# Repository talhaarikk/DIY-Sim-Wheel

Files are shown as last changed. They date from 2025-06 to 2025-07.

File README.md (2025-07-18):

# DIY Sim Wheel
## Purpose
The purpose of this project is to make a powerful sim racing wheel cheaply (also i like doing this kind of stuff). But actualy the main reason i started this project was that i didn't want to buy a logitech g29 (g29 because it is the most common, known, reliable and cheap model on the market). Because the g29 was made of too much plastic, the torque was not at the level i wanted and the size of the steering wheel was not enough for me. That's why i focused on these issues in my own design. Below you can find all the details of the steering wheel.  
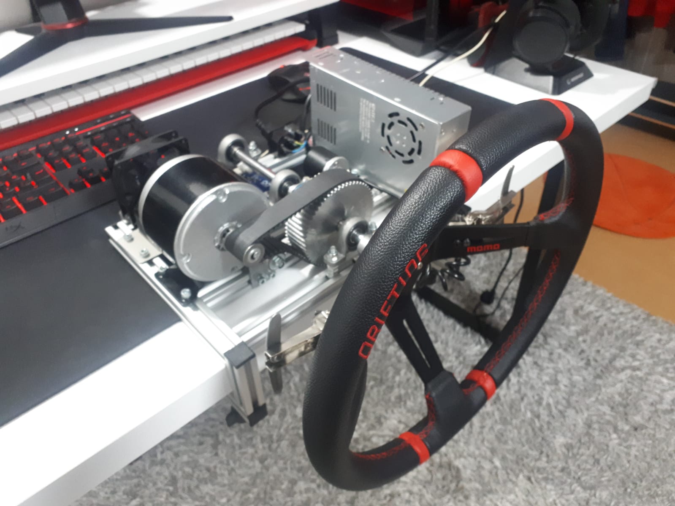
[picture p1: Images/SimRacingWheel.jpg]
Sim Racing Wheel
  
You can find more photos of the sim steering wheel in the Images/Steering_Wheel folder.  

## Motor
To be honest, when i started the project, i didn't want to make a design like the one below. I had in mind to make a direct drive sim wheel by purchasing a stepper motor with an encoder and a stepper motor driver. However, since the prices of these parts were higher ($110 for stepper motor and $110 for driver) and i couldn't see an example of a sim wheel made using with stepper motor, i decided to make this project with the motor below. My advice to you is that if you don't have a budget problem and still want to make your own sim wheel, you should continue with a servo motor. If I had used such a motor, i wouldn't have bothered with the gears, shaft or frame in this project.  
As an motor, i chose this motor which is originally used in scooters.  
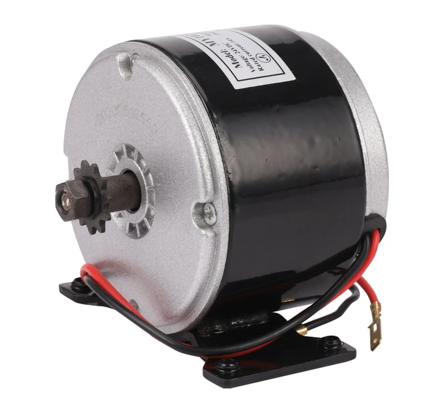
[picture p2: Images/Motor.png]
Motor
  
Brushed DC motor. Model: MY1025  
Works with 24V and 14A (so its 250W). Also 2750RPM (actually, what i paid attention to was not the rpm but the torque).  
I think this motor will be powerful enough for the steering wheel. If you want, you can do the project by using 2 smaller motor or even using 2 of this motor. Although i didn't need such a thing.
## Power Supply

When choosing a power supply, i preferred a 24V and 15A power supply. Since the motor is 250 watt, the watt of the power supply should be slightly higher (in this case 300W).  
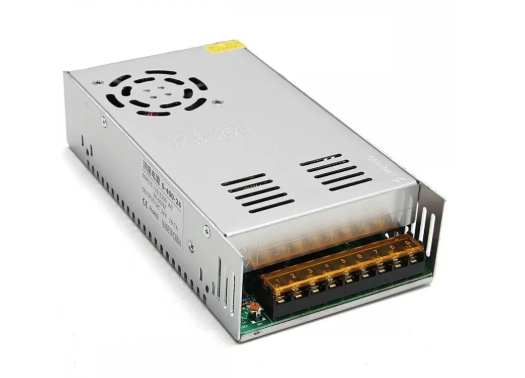
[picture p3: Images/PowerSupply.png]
Power Supply
  

## Gears
There are 4 gears in the steering wheel, one between the shaft and the motor and one between the shaft and the encoder. I recommend that you make sure that the gears are made of aluminum so that you can drill the holes and that they are not too heavy. Even though the gears were made of aluminum, the most challenging part of this project was the holes i drilled to mount the gears on the shaft. These gears mounted on the shaft should not be fixed with any gaps in order to ensure a healthy transmission. My method of fixing them was to drill screw holes in the gears and flatten the areas where the screws were tightened on the shaft to prevent them from slipping.  
  -**Components for the motor:**  
60-5M-25-AL (on the shaft)  
12-5M-25-AL (on the motor)  
410-5M-25 (pulley)  
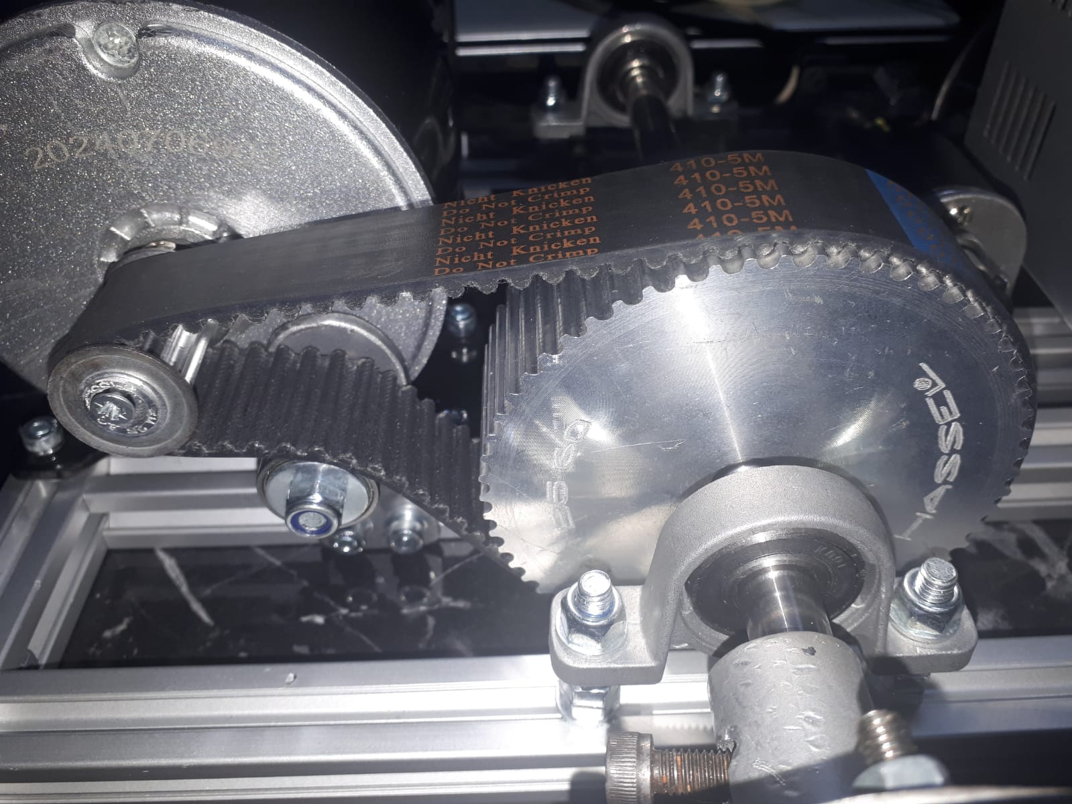
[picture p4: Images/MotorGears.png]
Motor Gears
  
The torque produced by the motor itself was around 0.87 nm. With the 60/12 gear ratio, this value was multiplied by 5, theoretically reaching 4.35 nm (i did not measure this value experimentally). This value is approximately twice that of the Logitech G29.  
  -**Components for the encoder:**  
12-3M-09-AL (on the encoder)  
30-3M-09-AL (on the shaft)  
192-3M-09 (pulley)  
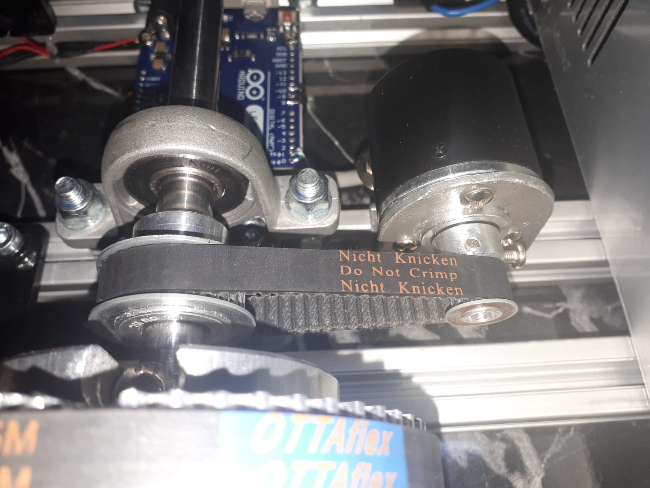
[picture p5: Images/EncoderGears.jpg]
Encoder Gears
  
Since the encoder itself will not transfer any torque and will only rotate the sensor, i did not feel the need to use a stronger belt as in the encoder. The encoder was reading 600 times in 1 turn. With the 12/30 gear ratio, this value increased by 2.5 times. Now the encoder is reading 1500 times in 1 turn. You can interpret this value as reading 1 every 0.25 degrees of steering wheel rotation, which is quite sufficient.  
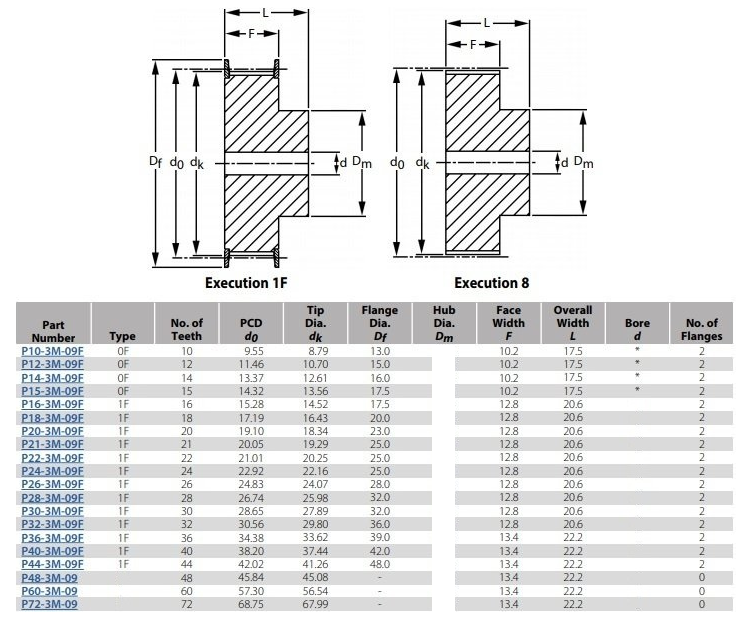
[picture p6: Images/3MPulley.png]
3M Pulley
  
Table of pulleys for size 3M-09. Unfortunately i couldn't find the one for 5M-25.  

## Other Hardwares
  -**Shaft**  
When talking about other components, i must first mention the shaft. The shaft length is 26 cm and its diameter is 12 mm. The material is stated as induction shaft, but if i were to choose the shaft again, i would definitely not choose this material. Drilling holes on it to fix the gears was a complete torture. At least it is solid now.  
  -**Bearing Housing**  
I used the following bearing to hold this shaft. Model number KP001. There are 3 of them holding the shaft, but you can also use 2 if you want.  
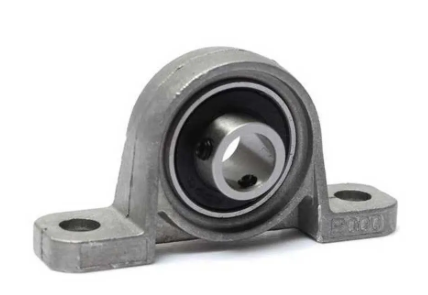
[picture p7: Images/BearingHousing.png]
Bearing Housing
  
  -**Belt Tensioner**  
For the belt tensioner, i used 3 bearings on a piece i cut from a metal plate. This piece both makes assembly easier and helps adjust the tension of the belt.  
  -**Steering Wheel**  
This is a after market steering wheel. Any one you like will do.  
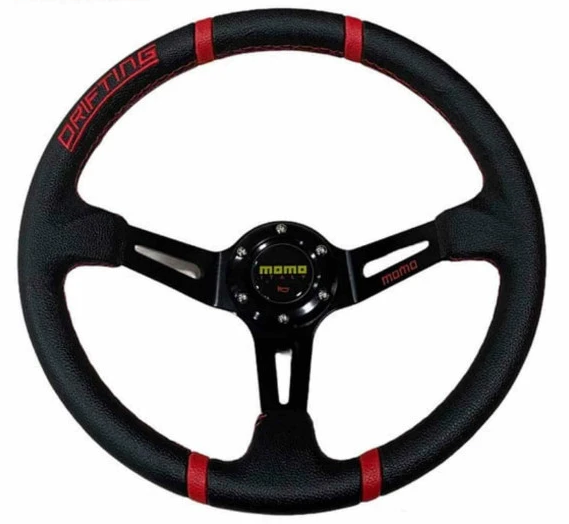
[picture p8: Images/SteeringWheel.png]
Steering Wheel
  
  -**Steering Wheel Hub**  
I made it by welding a pipe to a round metal plate. If you can, a 3D printed part would work just fine too.  
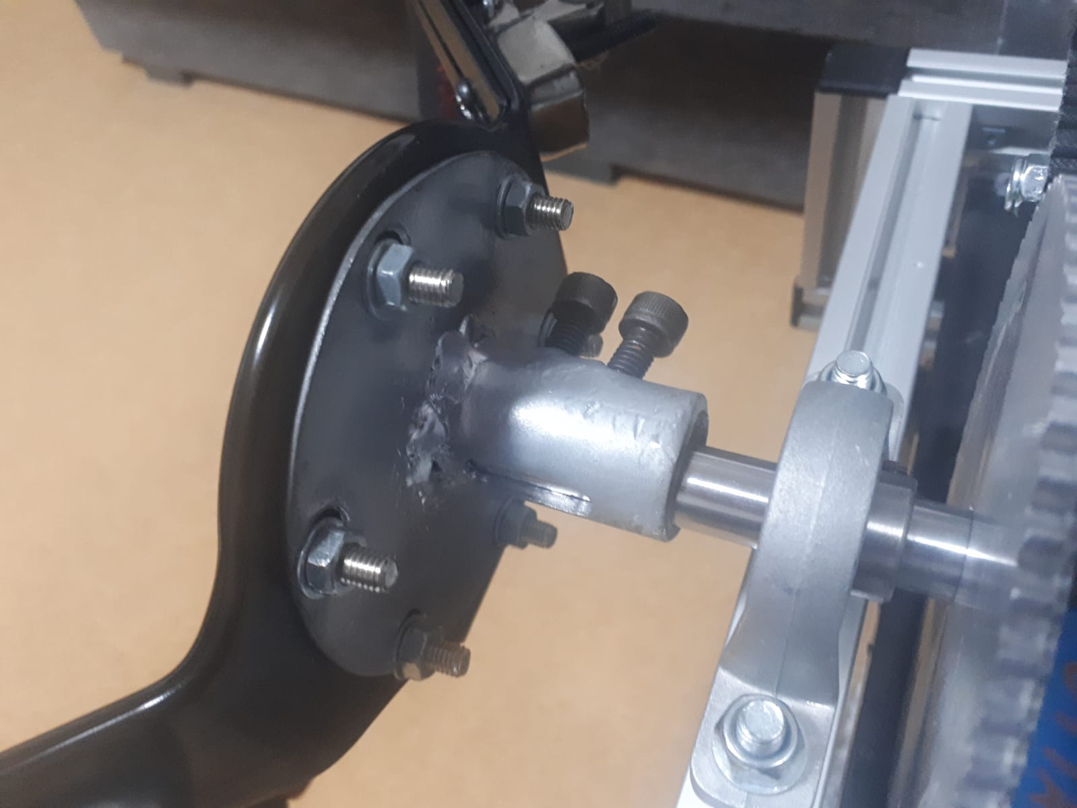
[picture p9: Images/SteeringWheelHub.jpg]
Steering Wheel Hub
  

## Frame
I used aluminum sigma profile in the cage structure that helps bring all the pieces together. Sigma profile width and length is 20 mm. The lengths of all the sigma profiles i use are as follows.  
280 mm x 4  
220 mm x 2  
70 mm x 2  
50 mm x 2  
The 70 and 50 mm pieces are a solution i found to fix the system to the table. If you have a sim racing cockpit, you won't need this part to fix it.  
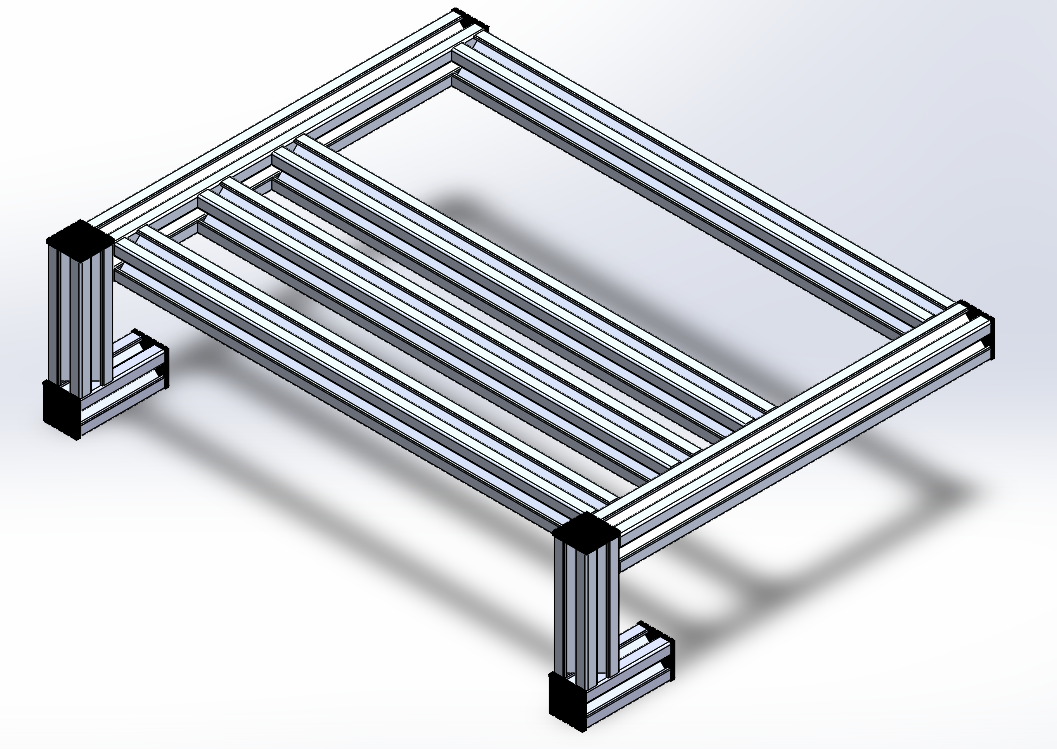
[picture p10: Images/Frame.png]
Frame
  
The bolts on the profile were used with imbus bolts and t-nuts for fixing. I used hidden corner joints to connect the profiles to each other. I also put caps on the ends of the profiles so that they would not look ugly.  

## Electronics
  -**Board**  
I chose Arduino Leonardo as the card in the project. Arduino Pro Micro will also do the same job, but Arduino Uno is not suitable for this project.  
  -**Motor Driver**  
I used the BTS7960B driver as the motor driver. This driver is enough to feed the motor, but i want to warn you about something. If the connections of this driver are made and the motor and encoder connections are not made yet, do not try to run the motor from the software. Don't ask how i know (i burned 2 of them).  
  -**Fan**  
Actually, i did not see that the motor and driver got very hot during use, but i still positioned a 5V computer fan to cool the motor and driver.  

## Design
I made the entire design using solidworks. I also found the gear diameters and belt lengths thanks to this program. You can find all the details of the project in these files. All files in the solidworks files section.  
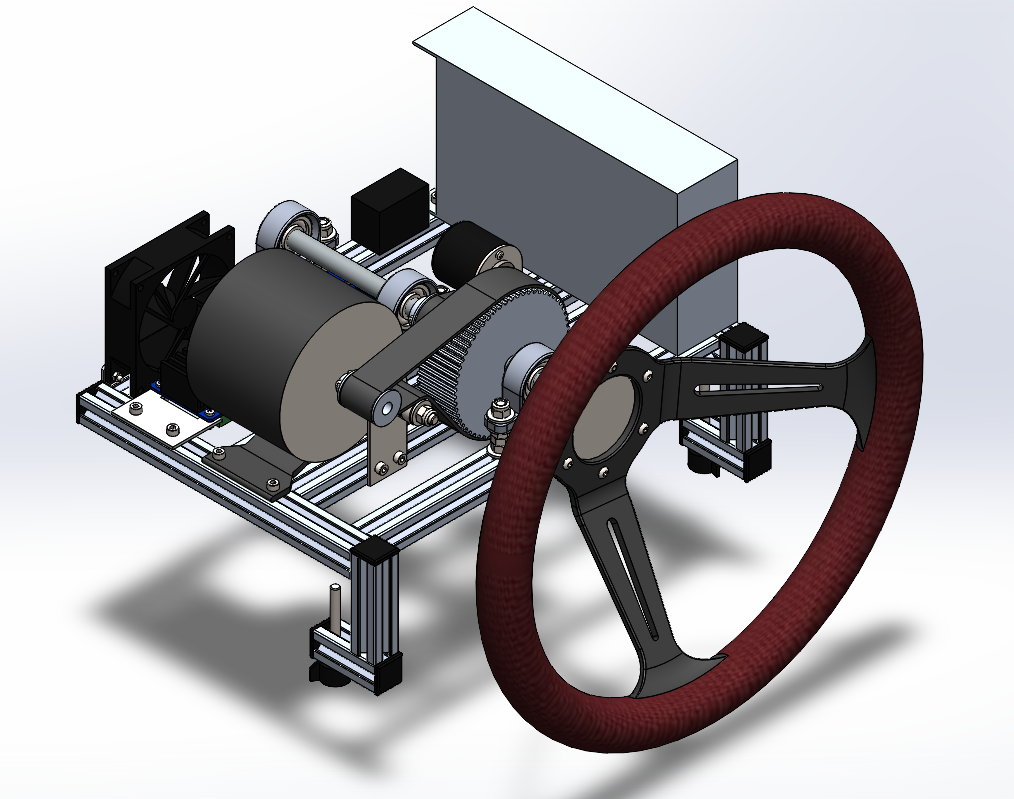
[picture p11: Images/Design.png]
Design
  
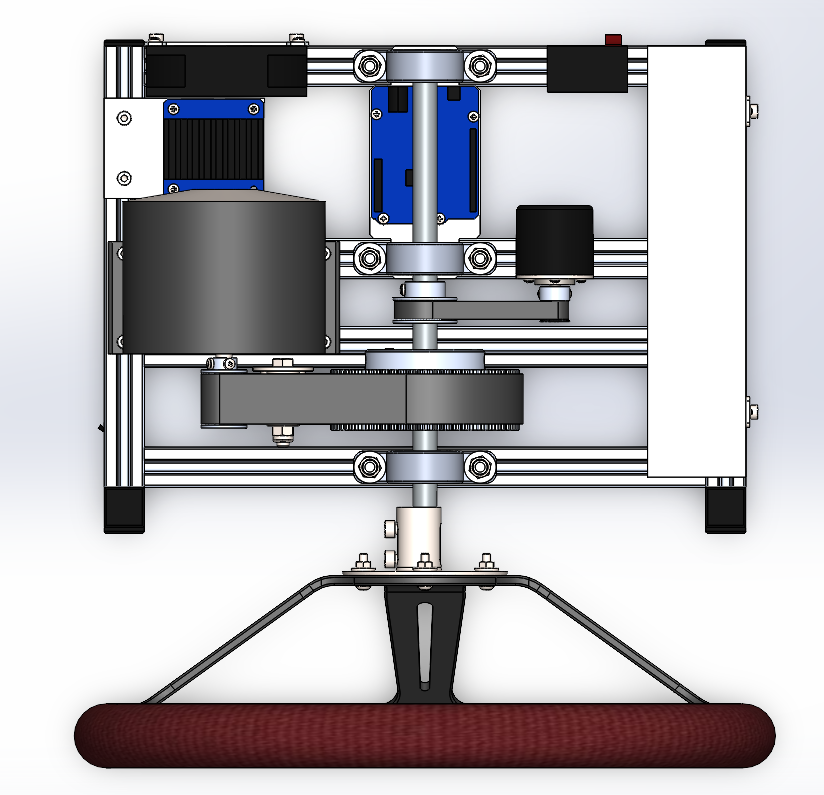
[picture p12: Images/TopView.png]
Top View
  
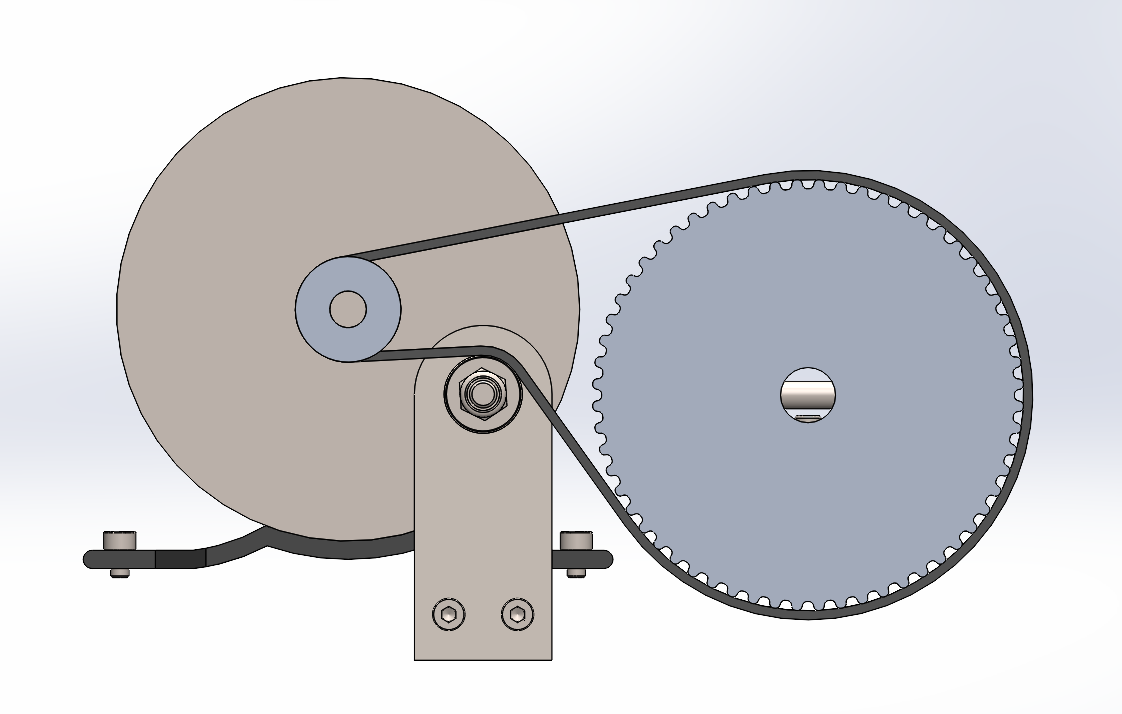
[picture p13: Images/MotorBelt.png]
Motor Belt
  
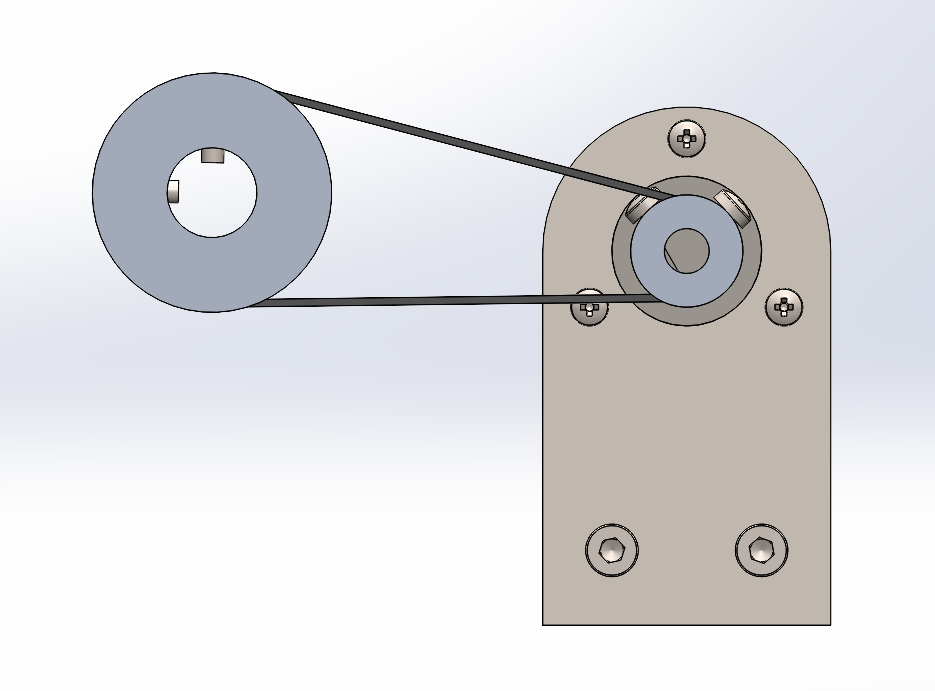
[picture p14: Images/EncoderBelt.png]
Encoder Belt
  

## Assembly
It is a bit difficult to assemble this whole system. The following steps can make it easier for you to understand the assembly.  
1-Assemble the entire frame structure and the elements on it except the encoder holder and the belt tensioner.  
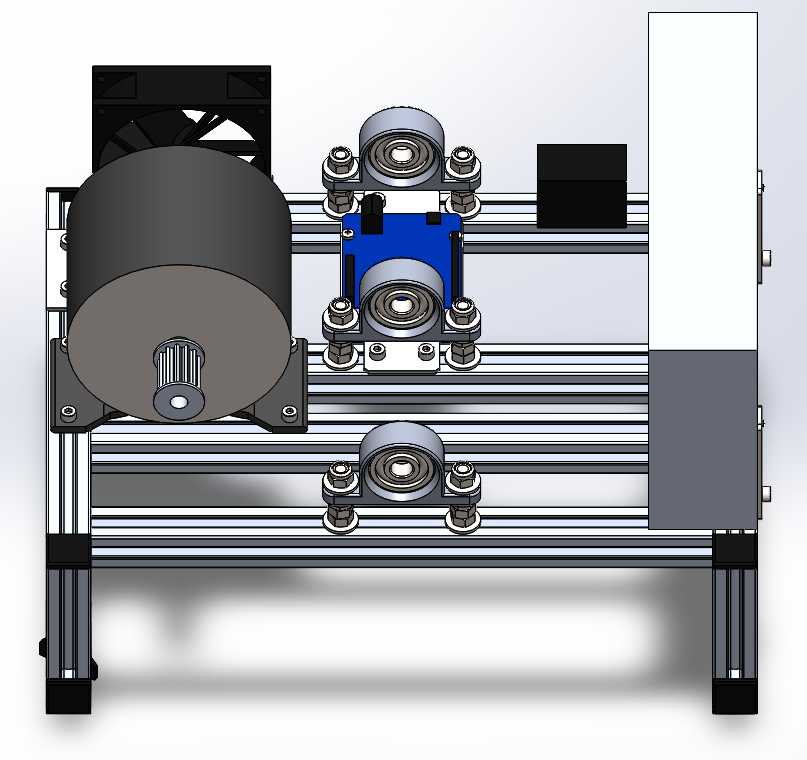
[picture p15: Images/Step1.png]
Step 1
  
2-Insert the shaft through the bearings one by one. Make sure the gears and belts remain inside the shaft when doing this.  
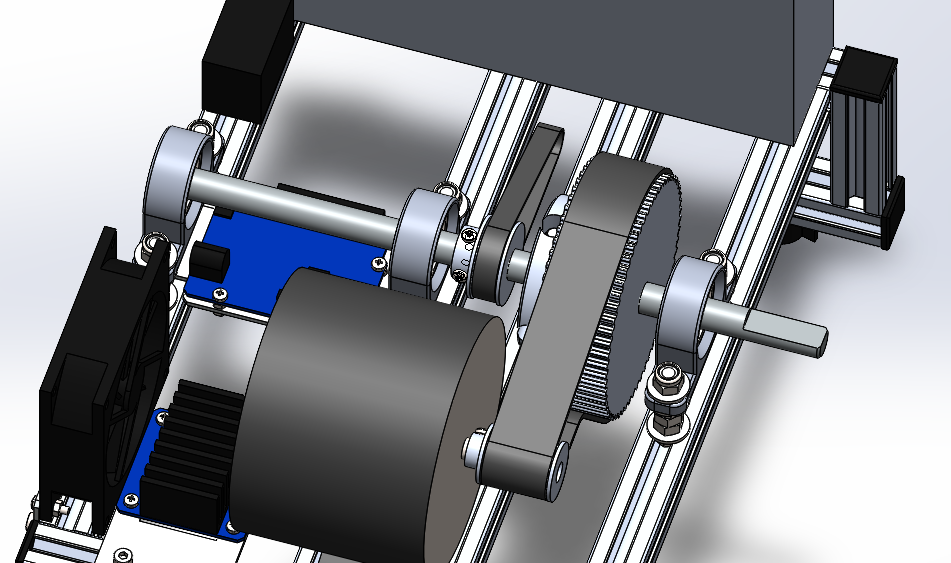
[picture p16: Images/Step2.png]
Step 2
  
3-Then tighten the bolts of the gears and connect them to the shaft.  
4-Install the encoder and belt tensioner. Then push these elements until the belts are at the appropriate tension and then tighten them.  
5-Finally, attach the steering wheel to the shaft.  

## Pedal Shifters
The reason i opened a separate title for the pedal shifter was that i decided to add it to the steering wheel after the whole project was finished. So this part is not in solidworks file. You don't have to do this part if you don't want to.  
I simply used a cabinet hinge as a pedal shifter. After cutting it to the required dimensions, i added a switch that is triggered when pressed. I made the connection to the arduino with a braided cable so that it can withstand the rotation of the steering wheel. This cable is removable and pluggable, so i can remove it when using manual gear. Other than these, there is nothing difficult about this part. You can understand how it works from the photo below.  
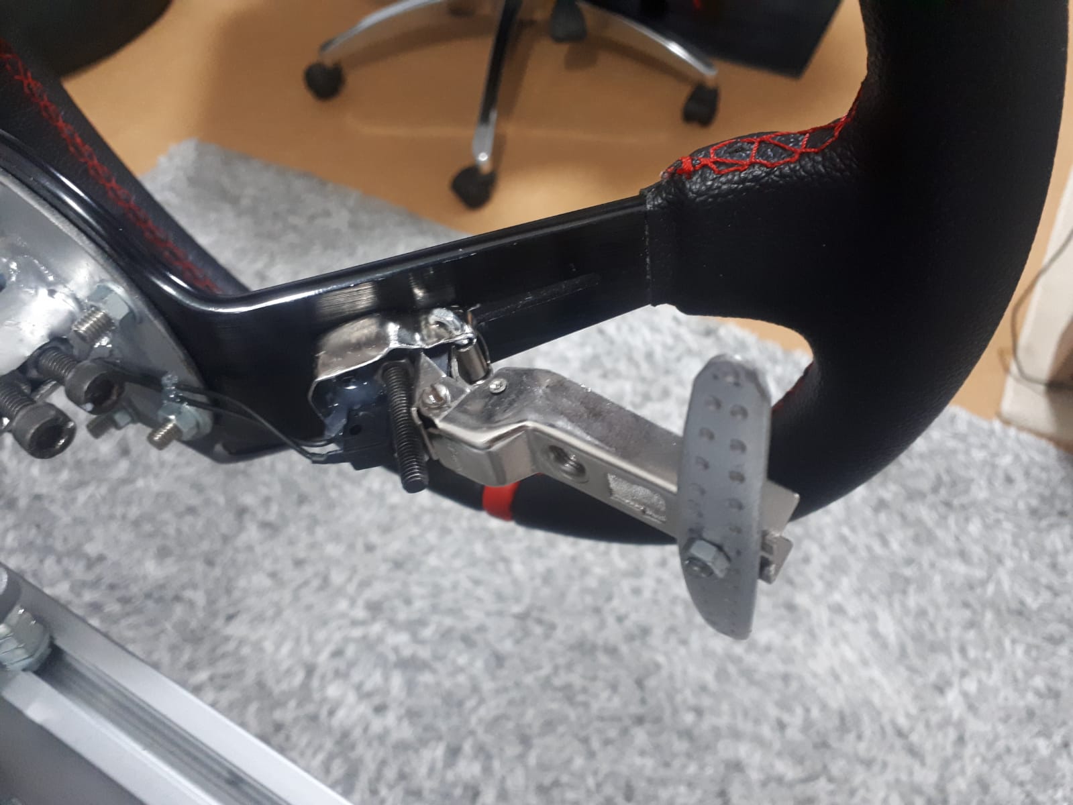
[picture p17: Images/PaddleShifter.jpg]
Paddle Shifter
  

## Wiring Diagram
The wiring is completely taken from the video below.  
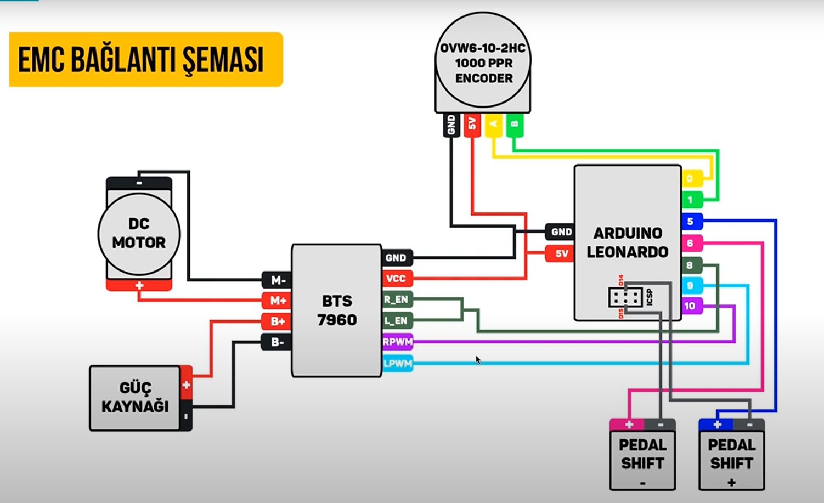
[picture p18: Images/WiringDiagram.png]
Wiring Diagram
  
The only difference in wiring is that you may need to reverse the motor + and - poles to the driver. That's what i had to do. Also in addition, i added an on/off switch and a power cable input to the + input of the power supply.  

## Software
Actually the first software i ran was the wheelconfig program but i couldn't get the system to work using this program. Also this program has a more complex schematic. That's why i preferred EMC software.  
The only thing i didn't do myself in this project and copied directly was the software. That's why i won't show how to set up the program, transfer it to arduino and make settings here. You can use the videos i put below to do these.  
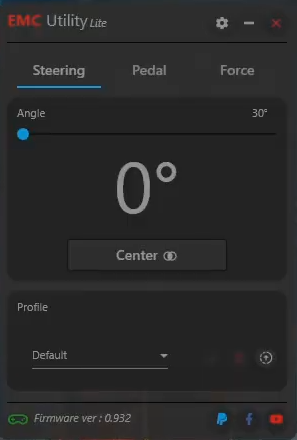
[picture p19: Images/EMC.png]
EMC
  
After installing the software, everything that needs to be done about the steering wheel is finished.  

## Cost
In this section, i will write the prices of the pieces in turkish lira. Since my purpose in doing my projects is completely up to my enjoyment, they are spread over a long period of time like 1-2 years. That's why prices and exchange rates are variable, but as of the date i did the project, you can think of 1 dollar as 30-40 turkish lira.  
Motor: 1700 tl  
Power supply: 600 tl  
Steering wheel: 1500 tl  
Encoder: 550 tl  
Arduino: 400 tl  
BTS7960b: 200 tl  
Gears: 1000 tl  
Other hardwares: 1000 tl  
Other electranics: 500 tl  
Total: 7450 tl  
Half price of g29.  

## Sources
Below are the videos that i watched to gain information when starting this project. I recommend that you watch them too.  
https://youtu.be/hbCjbCfUp0g?si=NynA37pT9rn3MCQu (for mechanical)  
https://youtu.be/FUZKslSwfaw?si=WwYVih52zpUwfXec (for electrical)  
https://youtu.be/L-FAyA0VQVQ?si=nJCx8VnmU1xidO3N  
https://youtu.be/nPorcXRC3Ns?si=enejoyd5WoKqs4ha  
https://youtu.be/aYYAbcPKN8g?si=kRVGH3cPVwXVqP0q  
https://youtu.be/gG_dbnKfH5Q?si=5sSKj9XNKsQQZj4X (example using stepper motor)  
https://youtu.be/_h417VxFmWQ?si=Obe5oXemXU2WvnzE (example using servo motor)  

## Conclusion
This project was an adventure that gave me a lot of knowledge while doing it (i can't say that i enjoyed it during the process). It was much more solid, powerful, cheap and high quality compared to other steering sets on the market. I hope i could contribute to your own projects. If you have any questions about the project, don't hesitate to ask me from talhaarik1965@gmail.com.

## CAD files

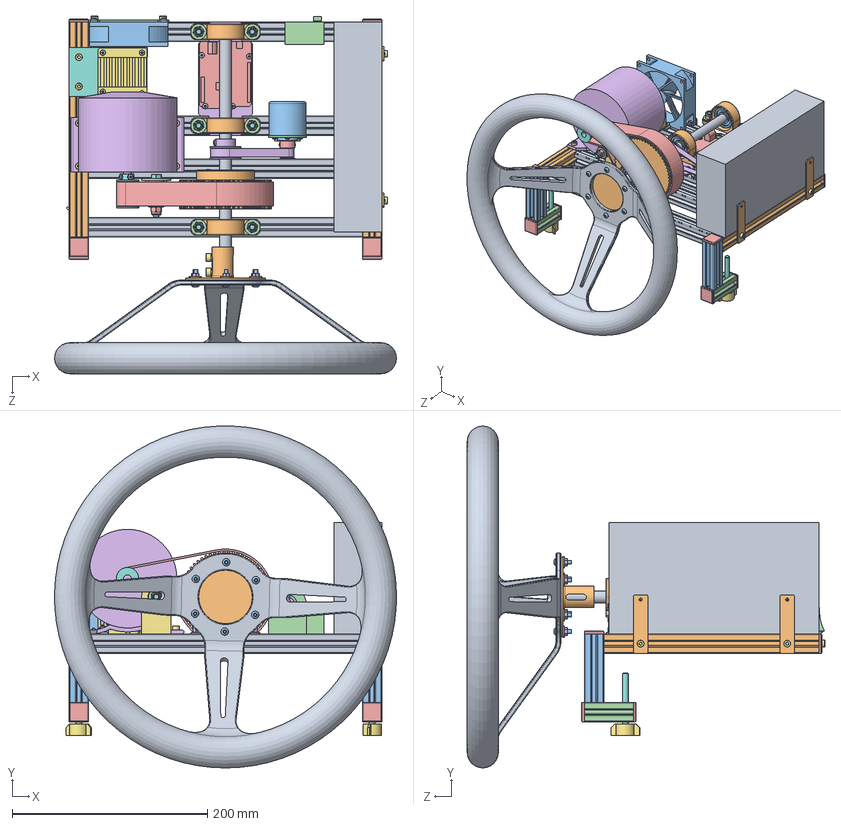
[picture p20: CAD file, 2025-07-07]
Solidworks Files/Assembly.SLDASM
349.9 x 349.8 x 366.0 mm
20x20 28cm Sigma Profile x 4
20x20 22cm Sigma Profile x 2
20x20 7cm Sigma Profile x 2
20x20 5cm Sigma Profile x 2
Sigma Cap x 8
hex nut style 1 gradeab_iso x 47
Table Mount x 2
hex bolt gradeb_iso x 9
Shaft
Bearing Housing x 3
instrument ball bearing_68_iso x 3
plain washer 10669 type nl_iso x 28
torque nut 01_iso x 7
Motor
socket head cap screw_iso x 23
12-5M-25-AL
pan head cross recess screw_iso x 20
60-5M-25-AL
Encoder
Encoder Holder
12-3M-09-AL
30-3M-09-AL
Belt Tensioner
angular contact ball bearing_68_iso x 3
Steering Wheel
Steering Wheel Hub
socket button head screw_iso x 6
Switch
Arduino Leonardo
Arduino Holder
BTS7960
Motor Driver Holder
Power Supply
Power Supply Holder x 2
Fan
Fan Holder
5M Belt
3M Belt

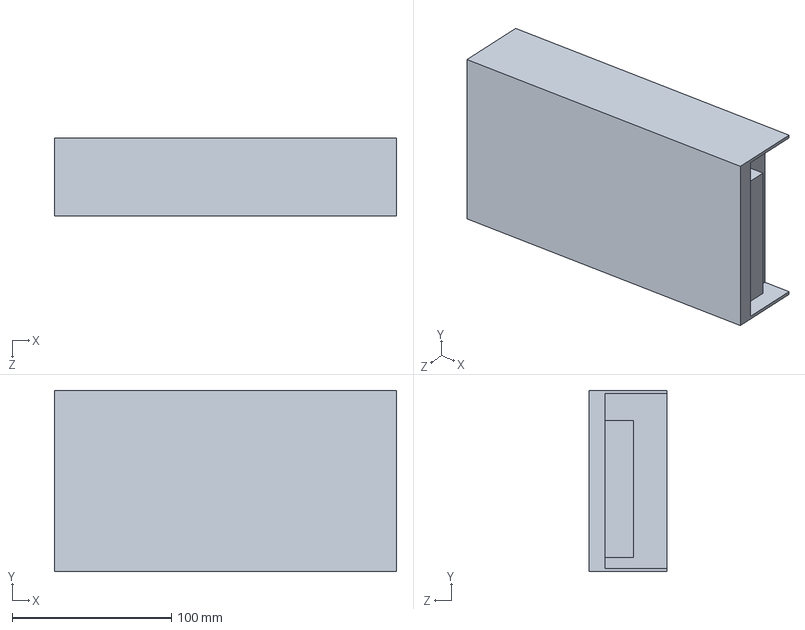
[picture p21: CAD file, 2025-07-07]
Solidworks Files/Power Supply.SLDPRT
215.0 x 114.0 x 49.0 mm

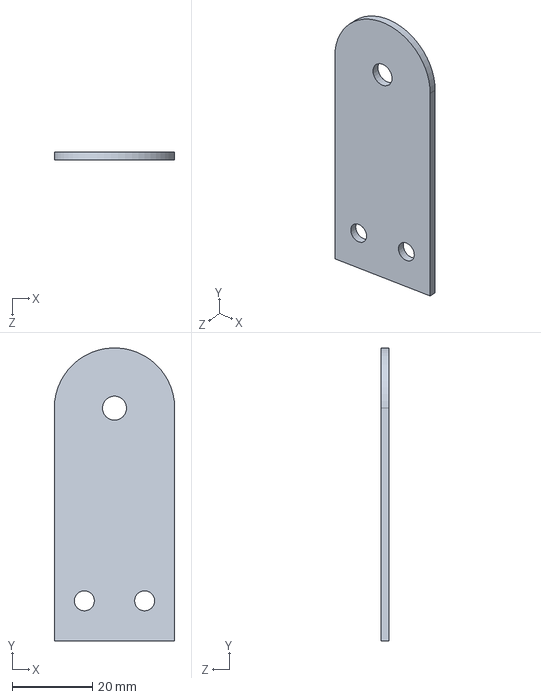
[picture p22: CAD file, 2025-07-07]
Solidworks Files/Belt Tensioner.SLDPRT
30.0 x 73.0 x 2.00 mm

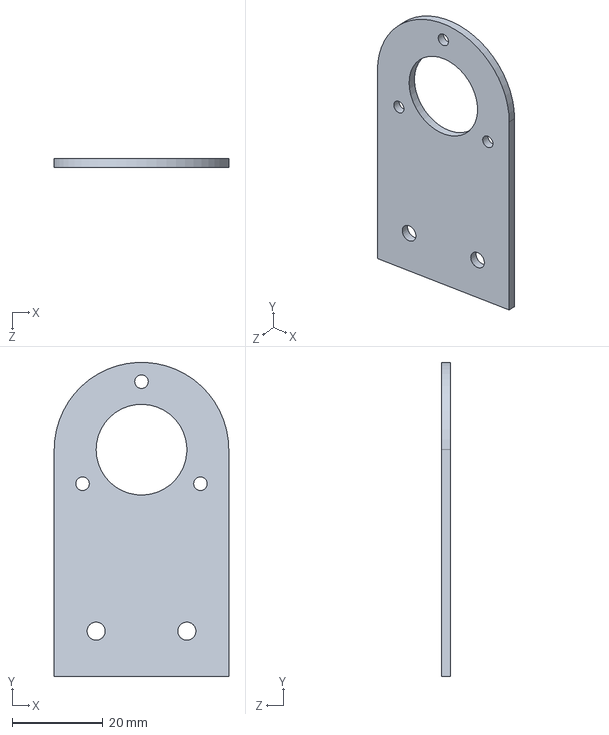
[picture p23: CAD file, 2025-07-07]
Solidworks Files/Encoder Holder.SLDPRT
38.5 x 69.2 x 2.00 mm

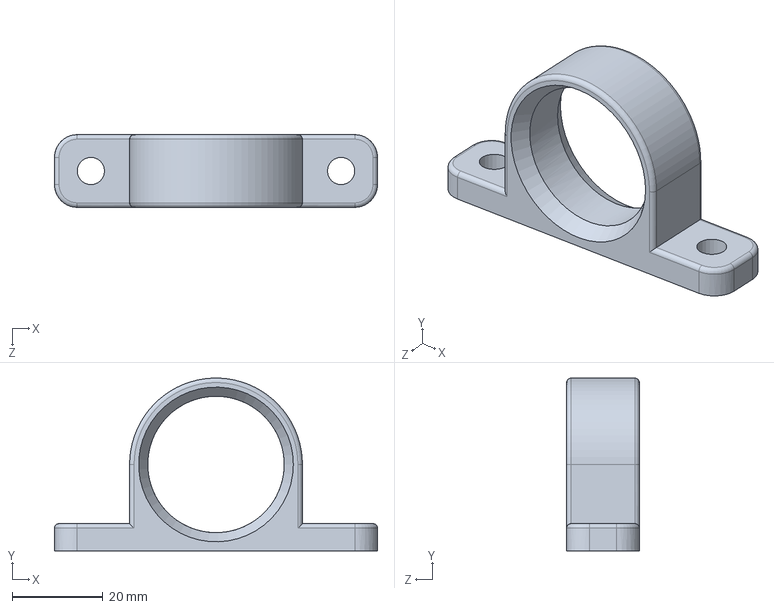
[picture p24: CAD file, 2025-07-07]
Solidworks Files/Bearing Housing.SLDPRT
71.0 x 38.0 x 16.0 mm

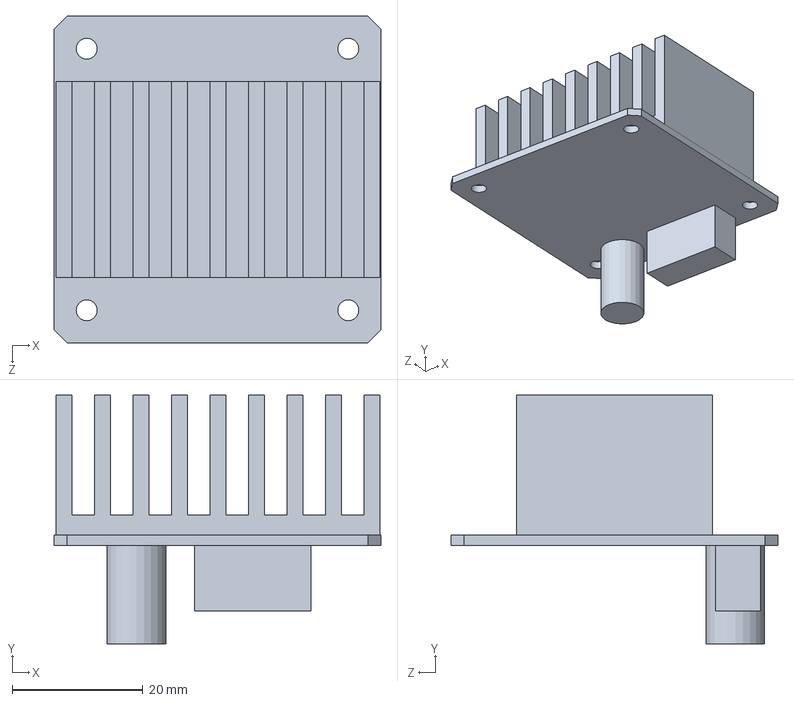
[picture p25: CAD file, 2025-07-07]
Solidworks Files/BTS7960.SLDPRT
50.0 x 38.0 x 50.0 mm

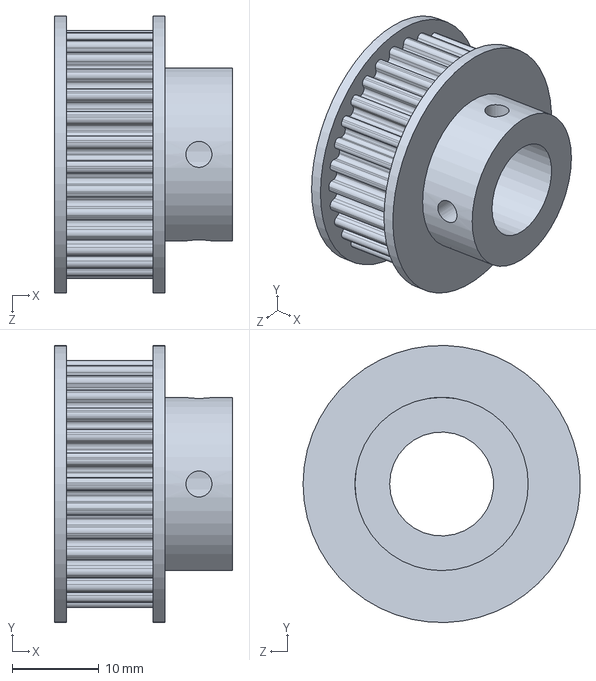
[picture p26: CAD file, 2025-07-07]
Solidworks Files/30-3M-09-AL.SLDPRT
20.6 x 32.0 x 32.0 mm

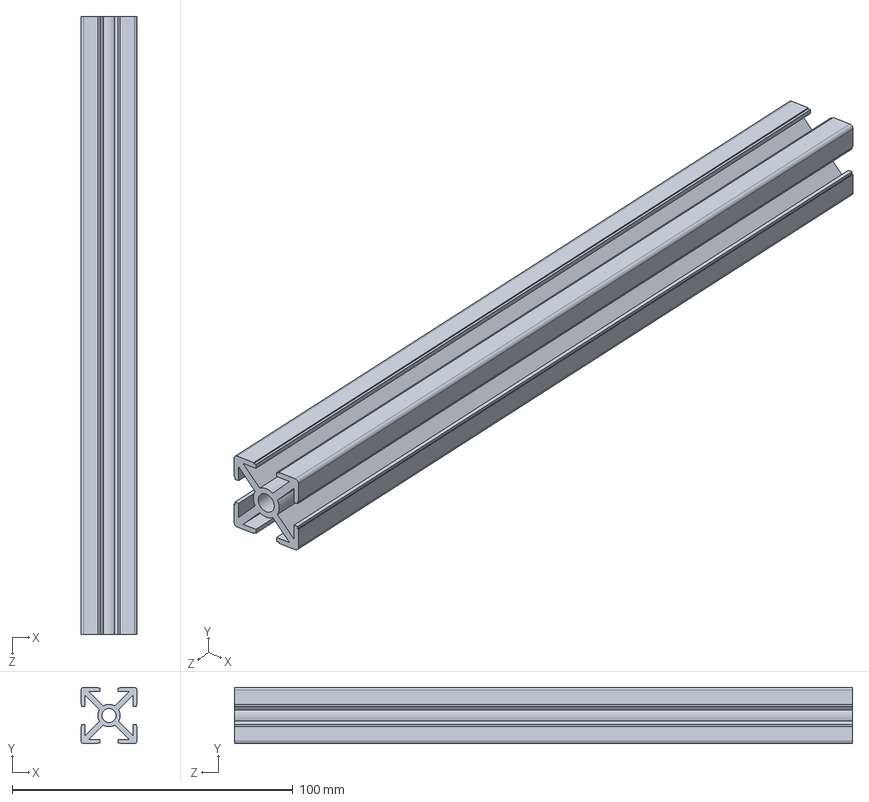
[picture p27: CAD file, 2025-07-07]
Solidworks Files/20x20 22cm Sigma Profile.SLDPRT
20.0 x 20.0 x 220.0 mm

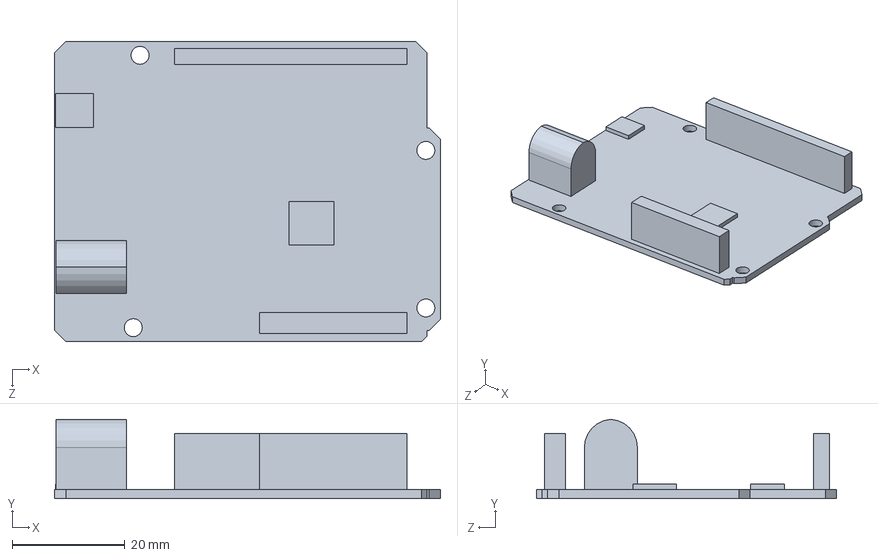
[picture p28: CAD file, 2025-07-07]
Solidworks Files/Arduino Leonardo.SLDPRT
68.6 x 14.1 x 53.4 mm

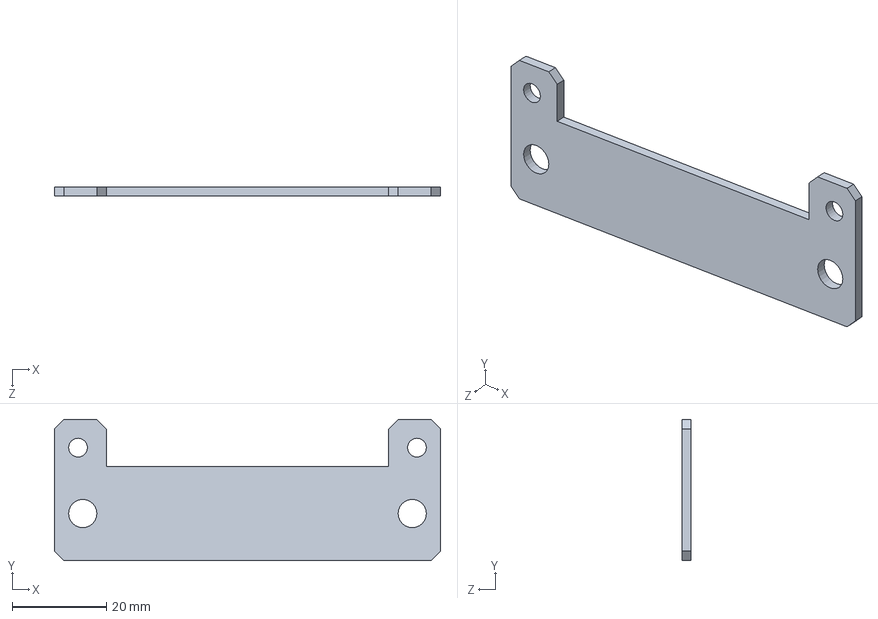
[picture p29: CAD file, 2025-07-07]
Solidworks Files/Fan Holder.SLDPRT
82.0 x 30.0 x 2.00 mm

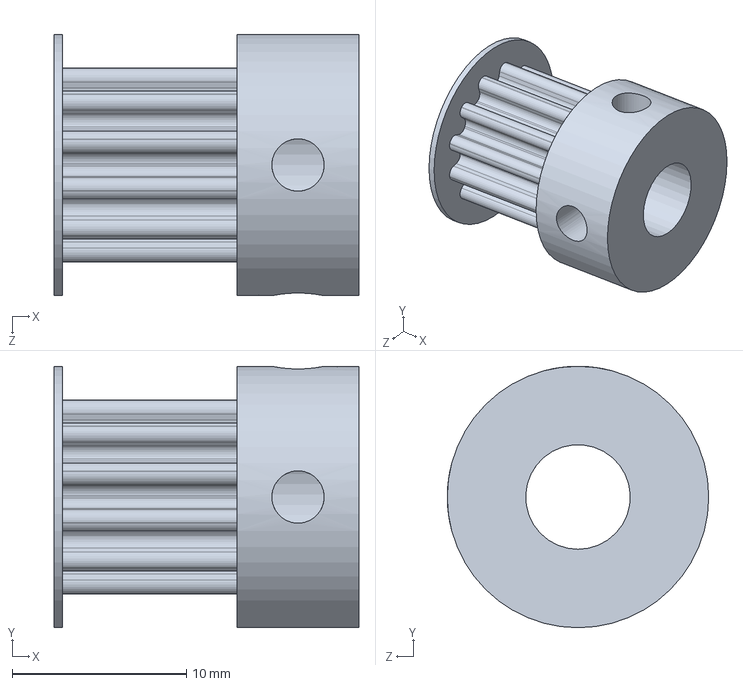
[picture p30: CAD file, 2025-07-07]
Solidworks Files/12-3M-09-AL.SLDPRT
17.5 x 15.0 x 15.0 mm

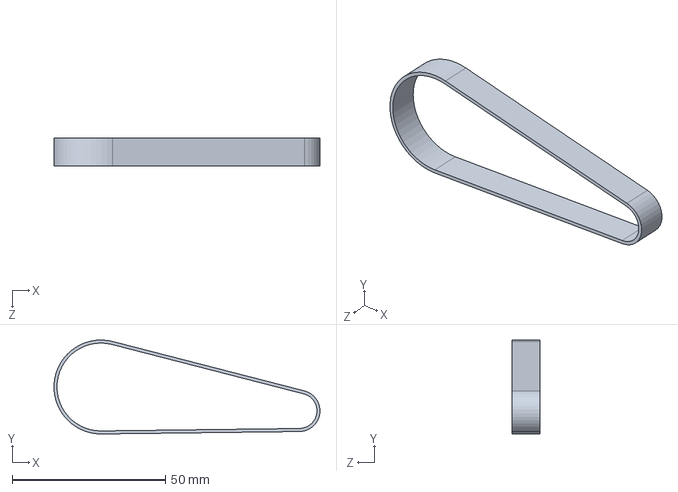
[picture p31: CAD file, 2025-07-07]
Solidworks Files/3M Belt.SLDPRT
86.8 x 30.7 x 9.00 mm

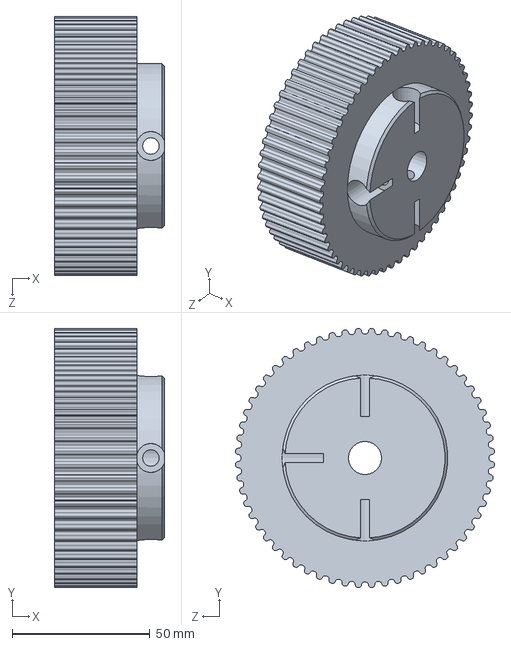
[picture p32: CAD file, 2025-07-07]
Solidworks Files/60-5M-25-AL.SLDPRT
40.0 x 93.9 x 93.9 mm

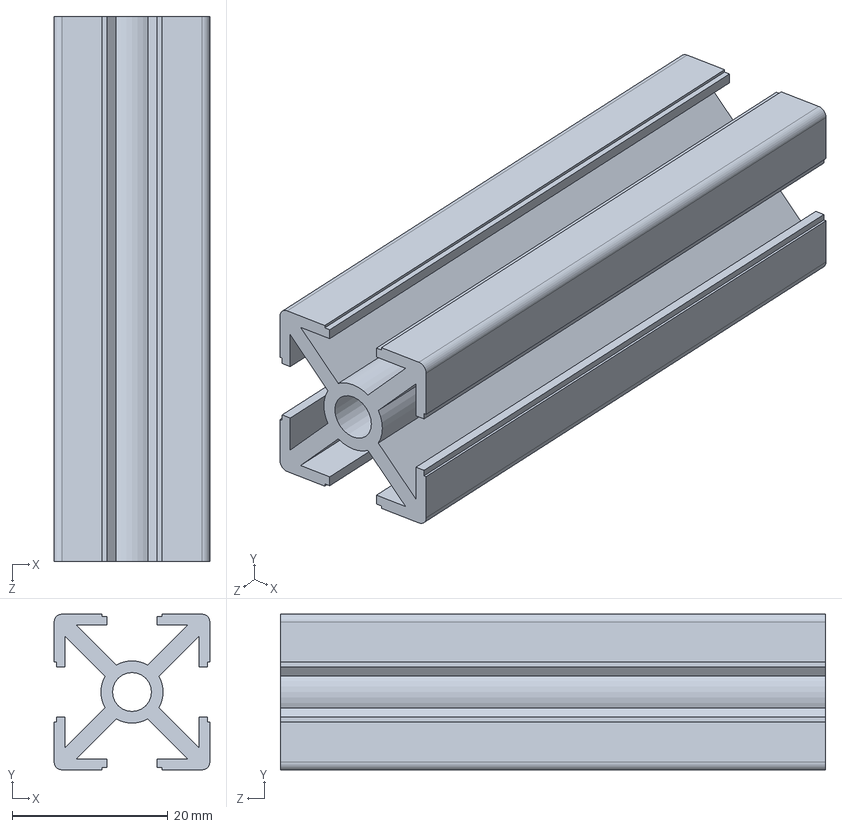
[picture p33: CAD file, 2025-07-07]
Solidworks Files/20x20 7cm Sigma Profile.SLDPRT
20.0 x 20.0 x 70.0 mm

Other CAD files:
Solidworks Files/Motor.SLDPRT
Solidworks Files/Encoder.SLDPRT
Solidworks Files/Sigma Cap.SLDPRT
Solidworks Files/Steering Wheel Hub.SLDPRT
Solidworks Files/12-5M-25-AL.SLDPRT
Solidworks Files/20x20 28cm Sigma Profile.SLDPRT
Solidworks Files/20x20 5cm Sigma Profile.SLDPRT
Solidworks Files/5M Belt.SLDPRT
Solidworks Files/Arduino Holder.SLDPRT
Solidworks Files/Fan.SLDPRT
Solidworks Files/Motor Driver Holder.SLDPRT
Solidworks Files/Power Supply Holder.SLDPRT
Solidworks Files/Shaft.SLDPRT
Solidworks Files/Steering Wheel.SLDPRT
Solidworks Files/Switch.SLDPRT
Solidworks Files/Table Mount.SLDPRT

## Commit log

2025-06-30 Rename Ekran görüntüsü 2025-06-30 215944.png to Motor.png
2025-06-30 Create Motor
2025-06-30 Rename Ekran görüntüsü 2025-06-30 222915.png to Motor.png
2025-07-02 Rename 3M Pulley.png to 3MPulley.png
2025-07-02 Rename Power Supply.png to PowerSupply.png
2025-07-02 Rename Steering Wheel.png to SteeringWheel.png
2025-07-06 Rename WhatsApp Görsel 2025-07-06 saat 13.16.37_abb980ff.jpg to MotorGears.png
2025-07-06 Rename WhatsApp Görsel 2025-07-06 saat 13.16.38_88f9be94.jpg to EncoderGears.jpg
2025-07-06 Rename Ekran görüntüsü 2025-07-06 135644.png to Frame.png
